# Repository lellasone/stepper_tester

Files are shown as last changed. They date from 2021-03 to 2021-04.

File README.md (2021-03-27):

# stepper_tester
This was a quick one-off stepper tester board. This version uses a TMC2208 from Trinamic. 

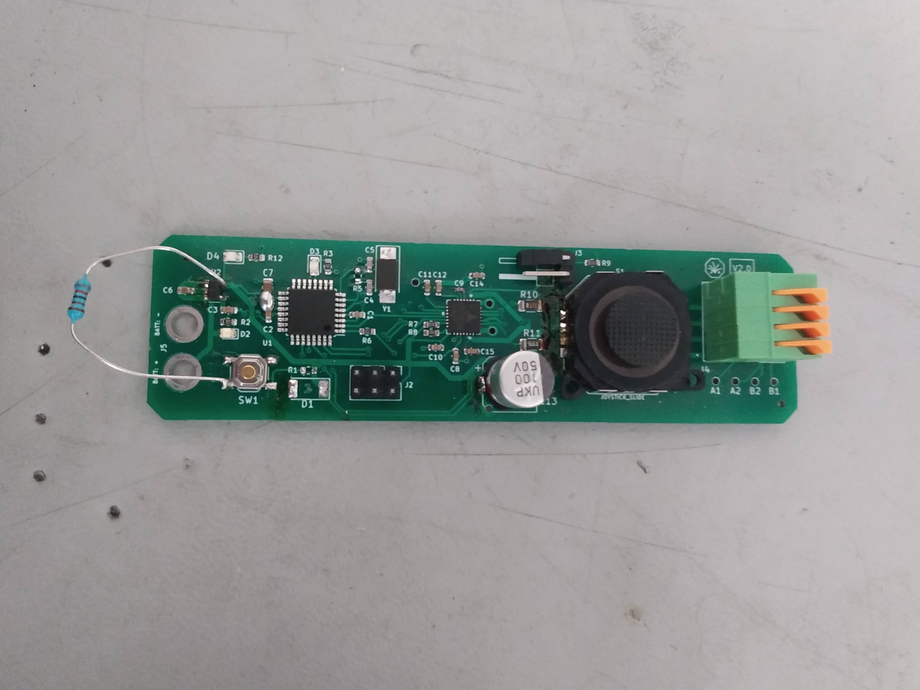
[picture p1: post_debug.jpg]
board just after debug


The idea for this version was to test out if the TMC2208 is really a drop in
replacement for it's competetors in practice (spoiler: it is!). A few (very)
minor improvements have been made to the code, but it actually ran with only
new pin mappings and no other changes the first time I uploaded it.

## Making Changes
For pcb design files look in PCB (KiCAD). For the arduino code look in the 
stepper_driver directory. 

You can upload code to the board using your ISP programmer of choice (I use 
tinyISP) with the fuse settings and pin mappings for a pro-mini.  

## Operating Instructions
* Move the joystick up and down to change the pulse frequency within a single micro-stepping band (zero centered).
* Flick the joystick side to side to change the microstepping level. (faster to the left)
    * To read the current microstepping level, count the status LED's pulses.
* To disable output, connect the jumper by the joystick.

## Firmware Depends
The sketch uses a few Arduino libraries (below) all of which can be 
installed from within the Arduino IDE using the standard library tool.
* PWM Freak - convenience functions for setting pwm devisor values. 
* TIMER1 - convenience functions for timer interrupts

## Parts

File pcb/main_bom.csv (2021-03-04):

Comment | Designator | Footprint | LCSC
100 nF | C1 | Capacitor_SMD:C_0603_1608Metric | C14663
0.1 uf | C10 | Capacitor_SMD:C_0603_1608Metric | C14663
0.22 uF | C11 | Capacitor_SMD:C_0603_1608Metric | C21120
100 uF | C13 | Capacitor_SMD:CP_Elec_8x10
0.1 uF | C2,C8,C12,C14,C15 | Capacitor_SMD:C_0603_1608Metric | C14663
10 nF | C3 | Capacitor_SMD:C_0603_1608Metric | C57112
22pF | C4,C5 | Capacitor_SMD:C_0603_1608Metric | C1653
1uF | C6 | Capacitor_SMD:C_0603_1608Metric | C15849
2.2 uF | C7 | Capacitor_SMD:C_0805_2012Metric | C49217
0.022 uF | C9 | Capacitor_SMD:C_0402_1005Metric | C1532
D | D1 | Diode_SMD:D_2010_5025Metric | C412437
LED | D2 | Diode_SMD:D_0603_1608Metric | C84256
LED | D3,D4 | Diode_SMD:D_0805_2012Metric | C2293
BATT + | J1 | BANANA_CONN
Conn_02x03_Odd_Even | J2 | Connector_PinHeader_2.54mm:PinHeader_2x03_P2.54mm_Vertical
Enable Jumper | J3 | Connector_PinHeader_2.54mm:PinHeader_1x02_P2.54mm_Horizontal
TBL003-254-04GR-2OR | J4 | footprints:header
BATT: - | J5 | BANANA_CONN
10k | R1,R7 | Resistor_SMD:R_0603_1608Metric | C22859
0.1 | R10,R11 | Resistor_SMD:R_1206_3216Metric | C25334
1.2k | R2,R6 | Resistor_SMD:R_0603_1608Metric | C22765
510 | R3,R12 | Resistor_SMD:R_0603_1608Metric | C23193
1M | R5 | Resistor_SMD:R_0603_1608Metric | C22935
100k | R8,R9 | Resistor_SMD:R_0603_1608Metric | C25803
JOYSTICK_SLIDE | S1 | sparkfun_switches:JOYSTICK-PSP1000
SW_Push | SW1 | Button_Switch_SMD:SW_SPST_TL3342
ATmega328P-AU | U1 | Package_QFP:TQFP-32_7x7mm_P0.8mm | C14877
LP2985-5.0 | U2 | Package_TO_SOT_SMD:SOT-23-5
TMC2208 | U3 | QFN28 | C115944
Crystal | Y1 | Crystal:Crystal_SMD_5032-2Pin_5.0x3.2mm_HandSoldering | C115962

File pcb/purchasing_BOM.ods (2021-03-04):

Part Numbers | Value | Footprint | Source | ID
C12, C10, C14, C15, C8, C1, C2 | 0.1uF | 603 | JLC | C14663 (https://lcsc.com/product-detail/Multilayer-Ceramic-Capacitors-MLCC-SMD-SMT_100nF-104-10-50V_C14663.html/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)
C3 | 10nF | 603 | JLC | C57112 (https://lcsc.com/product-detail/Multilayer-Ceramic-Capacitors-MLCC-SMD-SMT_10nF-103-10-50V_C57112.html/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)
C6 | 1uF | 603 | JLC | C15849 (https://lcsc.com/product-detail/Multilayer-Ceramic-Capacitors-MLCC-SMD-SMT_SAMSUNG_CL10A105KB8NNNC_1uF-105-10-50V_C15849.html/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)
C7 | 2.2uF | 805 | JLC | C49217 (https://lcsc.com/product-detail/Multilayer-Ceramic-Capacitors-MLCC-SMD-SMT_2-2uF-225-20-50V_C49217.html/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)
C9 | 0.022uF | 402 | JLC | C1532 (https://lcsc.com/product-detail/Multilayer-Ceramic-Capacitors-MLCC-SMD-SMT_22nF-223-10-50V_C1532.html/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)
C13 | 100uF | 8.3x8.3mm | Digikey | 1189-3099-2-ND
C11, | 0.22uF | 603 | JLC | C21120 (https://lcsc.com/product-detail/Multilayer-Ceramic-Capacitors-MLCC-SMD-SMT_SAMSUNG_CL10B224KA8NNNC_220nF-224-10-25V_C21120.html/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)
D3 | Blue LED | 805 | JLC | C2293
D2 | Red LED | 805 | JLC | C84256
D4 | Green LED | 805 | JLC | C63855
D1 | Protection Diode |  | JLC | C412437 (https://lcsc.com/product-detail/Diodes-Rectifiers-Fast-Recovery_MDD-Microdiode-Electronics-US1MG_C412437.html/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)
R10, R11 | 0.1Ohms | 1206 | JLC | C25334 (https://lcsc.com/product-detail/Chip-Resistor-Surface-Mount_Uniroyal-Elec-1206W4F100LT5E_C25334.html/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)
R1, R7 | 10k | 603 | JLC | C22859 (https://lcsc.com/product-detail/Chip-Resistor-Surface-Mount_Uniroyal-Elec-0603WAF100JT5E_C22859.html/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)
C4, C5, | 22pF | 603 | JLC | C1653 (https://lcsc.com/product-detail/Multilayer-Ceramic-Capacitors-MLCC-SMD-SMT_SAMSUNG_CL10C220JB8NNNC_22pF-220-5-50V_C1653.html/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)
R12, R3 | 510Ohms | 603 | JLC | C23193 (https://lcsc.com/product-detail/Chip-Resistor-Surface-Mount_Uniroyal-Elec-0603WAF5100T5E_C23193.html/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)
R2, R6 | 1.2k | 603 | JLC | C22765 (https://lcsc.com/product-detail/Chip-Resistor-Surface-Mount_Uniroyal-Elec-0603WAF1201T5E_C22765.html/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)
R5 | 1M | 603 | JLC | C22935 (https://lcsc.com/product-detail/Chip-Resistor-Surface-Mount_Uniroyal-Elec-0603WAF1004T5E_C22935.html/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)
R8, R9 | 100k | 603 | JLC | C25803 (https://lcsc.com/product-detail/Chip-Resistor-Surface-Mount_Uniroyal-Elec-0603WAF1003T5E_C25803.html/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)
S1 | Slide Joystick |  | Digikey | 1568-1848-ND
U1 | 328p | TQFP-32_7.0x7.0x0.8P | JLC | C14877 (https://lcsc.com/product-detail/ATMEL-AVR_ATMEL_ATMEGA328P-AU_ATMEGA328P-AU_C14877.html/?href=jlc-SMT)
U3 | TMC2208 | QFN-28_EP_5.0x5.0x0.5P | JLC | C115944 (https://lcsc.com/product-detail/Motor-Drivers_TRINAMIC_TMC2208-LA-T_TMC2208-LA-T_C115944.html/?href=jlc-SMT)
U2 | LP2985-5.0 | SOT23 | Digikey | LP2985AIM5-5.0
Y1 | Crystal | SMD-5032_2P | JLC | C115962 (https://lcsc.com/product-detail/SMD-Crystal-Resonators_Yangxing-Tech-X50328MSB2GI_C115962.html/?href=jlc-SMT)
J2 | 2x3 pin header | 2.54mm | Digikey | 952-2121-ND
J3 | 1x2 bent headder | 2.54mm | Home | Already Have
J4 | 1x4 snap | 2.54mm | Digikey | 102-6387-ND
Jumper | Jumpuer | 2.54mm | Digikey | 952-2165-ND‎
Increase 5V buss width.

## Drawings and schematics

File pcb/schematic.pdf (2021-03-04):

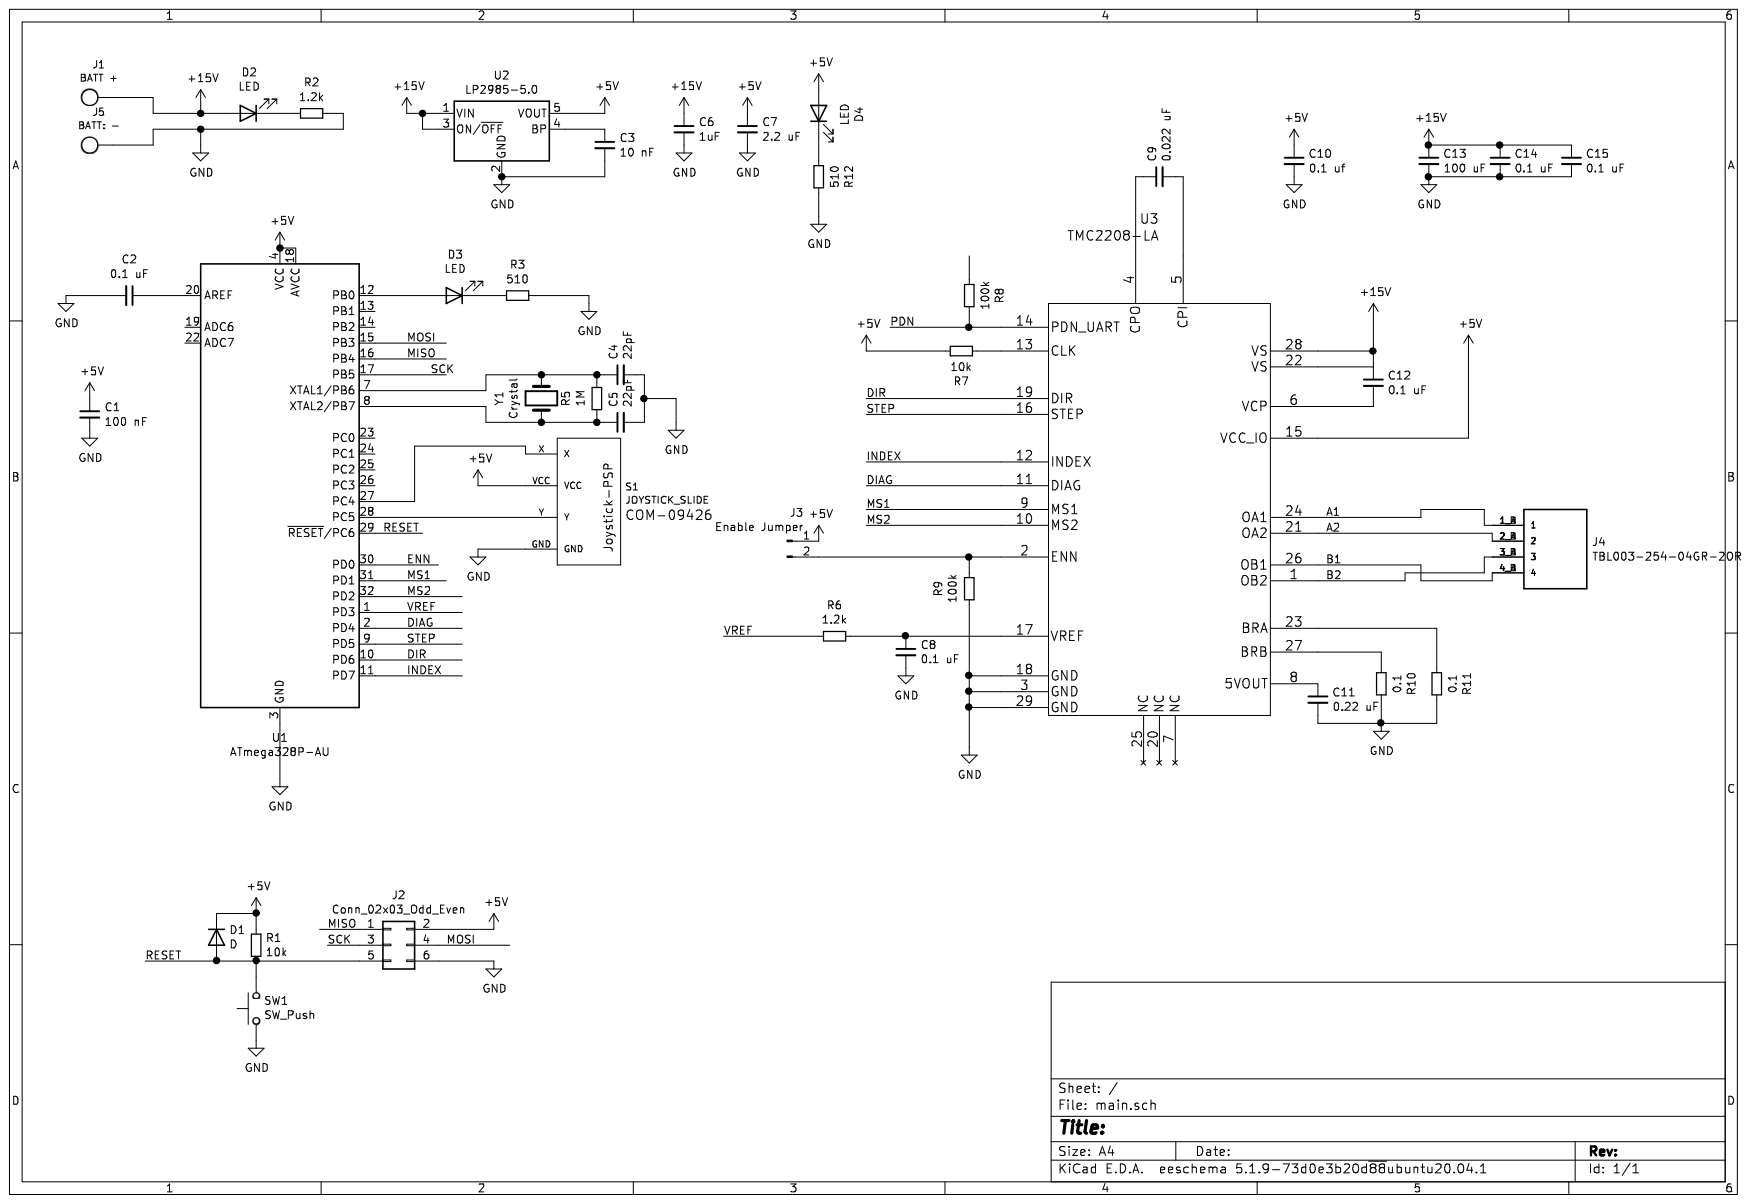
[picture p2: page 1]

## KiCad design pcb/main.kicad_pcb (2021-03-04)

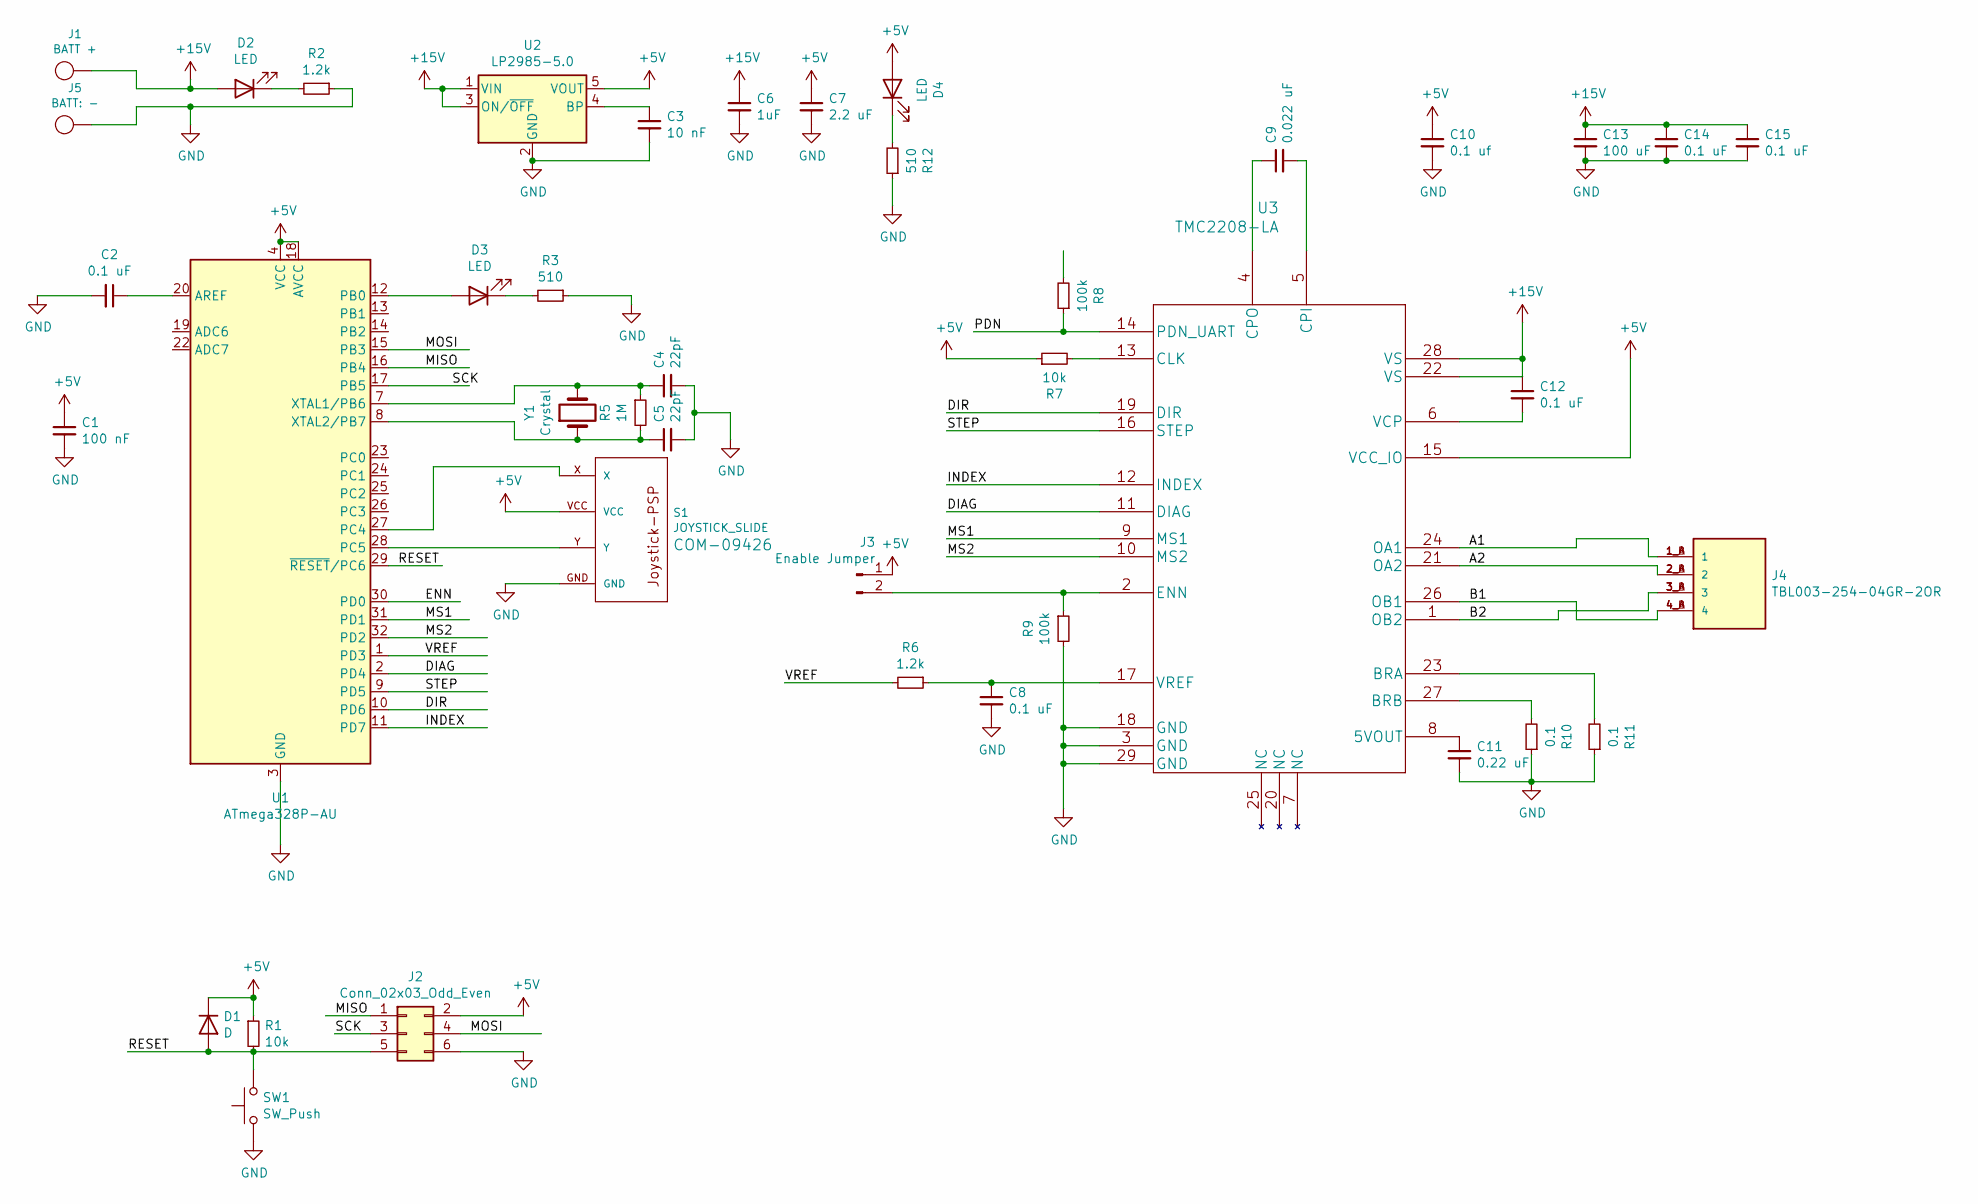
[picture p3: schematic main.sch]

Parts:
C1: 100 nF; C_0603_1608Metric; LCSC C14663
C2, C8, C12, C14, C15: 0.1 uF; C_0603_1608Metric; LCSC C14663
C3: 10 nF; C_0603_1608Metric; LCSC C57112
C4, C5: 22pF; C_0603_1608Metric; LCSC C1653
C6: 1uF; C_0603_1608Metric; LCSC C15849
C7: 2.2 uF; C_0805_2012Metric; LCSC C49217
C9: 0.022 uF; C_0402_1005Metric; LCSC C1532
C10: 0.1 uf; C_0603_1608Metric; LCSC C14663
C11: 0.22 uF; C_0603_1608Metric; LCSC C21120
C13: 100 uF; CP_Elec_8x10
D1: D; D_2010_5025Metric; LCSC C412437
D2: LED; D_0603_1608Metric; LCSC C84256
D3: LED; D_0805_2012Metric; LCSC C2293
D4: LED; D_0805_2012Metric; LCSC C63855
J1: BATT +; BANANA_CONN
J2: Conn_02x03_Odd_Even; PinHeader_2x03_P2.54mm_Vertical
J3: Enable Jumper; PinHeader_1x02_P2.54mm_Horizontal
J4: TBL003-254-04GR-2OR; header
J5: BATT: -; BANANA_CONN
R1, R7: 10k; R_0603_1608Metric; LCSC C22859
R2, R6: 1.2k; R_0603_1608Metric; LCSC C22765
R3, R12: 510; R_0603_1608Metric; LCSC C23193
R5: 1M; R_0603_1608Metric; LCSC C22935
R8, R9: 100k; R_0603_1608Metric; LCSC C25803
R10, R11: 0.1; R_1206_3216Metric; LCSC C25334
S1: JOYSTICK_SLIDE; JOYSTICK-PSP1000
SW1: SW_Push; SW_SPST_TL3342
U1: ATmega328P-AU; TQFP-32_7x7mm_P0.8mm; LCSC C14877
U2: LP2985-5.0; SOT-23-5
U3: TMC2208-LA; LCSC C115944
Y1: Crystal; Crystal_SMD_5032-2Pin_5.0x3.2mm_HandSoldering; LCSC C115962

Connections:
+5V: C1.1, C7.1, C10.1, D1.1 (K), D4.2 (A), J2.2, J3.1, R1.1, R7.1, S1.VCC, U1.4 (VCC), U1.6 (VCC), U1.18 (AVCC), U2.5 (VOUT), U3.15 (VCC_IO)
+15V: C6.1, C12.1, C13.1, C14.1, C15.1, D2.2 (A), J1.1, U2.1 (VIN), U2.3 (ON/~OFF~), U3.22 (VS), U3.28 (VS)
/A1: J4.1_A (1), J4.1_B (1), U3.24 (OA1)
/A2: J4.2_A (2), J4.2_B (2), U3.21 (OA2)
/B1: J4.4_A (4), J4.4_B (4), U3.26 (OB1)
/B2: J4.3_A (3), J4.3_B (3), U3.1 (OB2)
/DIAG: U1.2 (PD4), U3.11 (DIAG)
/DIR: U1.10 (PD6), U3.19 (DIR)
/ENN: U1.30 (PD0)
/INDEX: U1.11 (PD7), U3.12 (INDEX)
/MISO: J2.1, U1.16 (PB4)
/MOSI: J2.4, U1.15 (PB3)
/MS1: U1.31 (PD1), U3.9 (MS1)
/MS2: U1.32 (PD2), U3.10 (MS2)
/PDN: R8.1, U3.14 (PDN_UART)
/RESET: D1.2 (A), J2.5, R1.2, SW1.2, U1.29 (~RESET~/PC6)
/SCK: J2.3, U1.17 (PB5)
/STEP: U1.9 (PD5), U3.16 (STEP)
/VREF: R6.2, U1.1 (PD3)
GND: C1.2, C2.2, C3.2, C4.2, C5.2, C6.2, C7.2, C8.2, C10.2, C11.2, C13.2, C14.2, C15.2, J2.6, J5.1, R2.1, R3.1, R9.2, R10.1, R11.1, R12.1, S1.GND, SW1.1, U1.3 (GND), U1.5 (GND), U1.21 (GND), U2.2 (GND), U3.3 (GND), U3.18 (GND), U3.29 (GND)
unnamed: C2.1, U1.20 (AREF)
unnamed: C3.1, U2.4 (BP)
unnamed: C4.1, R5.1, U1.7 (XTAL1/PB6), Y1.2
unnamed: C5.1, R5.2, U1.8 (XTAL2/PB7), Y1.1
unnamed: C8.1, R6.1, U3.17 (VREF)
unnamed: C9.1, U3.4 (CPO)
unnamed: C9.2, U3.5 (CPI)
unnamed: C11.1, U3.8 (5VOUT)
unnamed: C12.2, U3.6 (VCP)
unnamed: D2.1 (K), R2.2
unnamed: D3.1 (K), R3.2
unnamed: D3.2 (A), U1.12 (PB0)
unnamed: D4.1 (K), R12.2
unnamed: J3.2, R9.1, U3.2 (ENN)
unnamed: R7.2, U3.13 (CLK)
unnamed: R10.2, U3.27 (BRB)
unnamed: R11.2, U3.23 (BRA)
unnamed: S1.X, U1.27 (PC4)
unnamed: S1.Y, U1.28 (PC5)

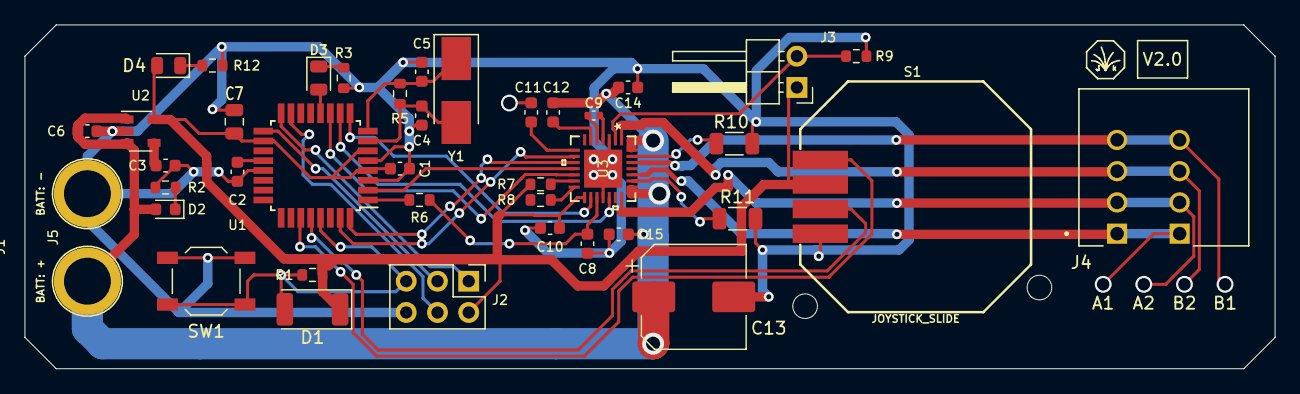
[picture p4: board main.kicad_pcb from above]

Board: 2 copper layers, 101.6 x 27.9 mm, 41 parts (0 on the bottom side), 38 nets.

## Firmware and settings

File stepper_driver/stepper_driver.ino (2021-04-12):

/* 
 *  This is some quick and dirty drive code for my stepper
 *  tester board. It allows speed control and step size 
 *  control based on the joystick, with an expontential 
 *  on the throttle to make control a bit nice. 
 *  
 *  Controls: 
 *  As designed, the stepper tester has throttle
 *  control along it's long axis, with an exponential gain
 *  and a small deadband in the middle. 
 *  
 *  Microstepping is controlled using the short axis, movements
 *  fully to the right will cause an increase in micro-stepping
 *  resulution (if possible) while movements to the left will
 *  cause a decrease. Note that the joystick must return to it's
 *  zero position before another command will be registered. 
 *  
 *  Update: 3/3/2021: Changed pin-mapping to match new board.
 *                    Program with pro-mini settings.
 *  Maintainer: Jake Ketchum
 */

#include "TimerOne.h"

// Hardware Pinouts.
#define PIN_TX     -1
#define PIN_RX     -1
#define PIN_STEP   5
#define PIN_DIR    6
#define PIN_RESET  -1 // reset device, optional. (Not Used)
#define PIN_SLEEP  -1 // dissables output, optional. (Not Used)
#define PIN_FAULT  -1 // should be pulled up. (Not Used)
#define PIN_DECAY  -1
#define PIN_ENABLE 0
#define PIN_HOME   -1 // should be pulled up. (Not Used)
#define PIN_VREF   3
#define PIN_MODE0  1
#define PIN_MODE1  2
#define PIN_MODE2  -1 //(Not Used)
#define PIN_THROTTLE A5
#define PIN_AUX A4
#define PIN_LED 8

// Chip configuration defaults
#define DEFAULT_MODE 0x03
#define DEFAULT_CURRENT 1.7
#define DEFAULT_DECAY HIGH
#define DEFAULT_DIR false

#define CURRENT_MIN 0
#define CURRENT_MAX 2

#define MODE_MIN 0x00
#define MODE_MAX 0x03

#define CURRENT_SENSE_RESISTOR 0.1

#define DEADBAND_HALF 20
#define DEADBAND_CENTER 522



//set the scaling endpoints for the throttle joystick. 
#define THROTTLE_MAX 825
#define THROTTLE_MIN 235 
#define MAX_ACCEL   .25 //The maximum acceleration allowed in rps/s
#define STEPS_PER_REV 200.0 //steps per revolution of the motor.
                          //Scales MAX_ACCEL.
#define MICROS_PER_SECOND 1000000.0

// Speed limits. (rotations per second)
#define MAX_VEL 1.5
#define MIN_VEL 0.1

// Timing defines. 
#define PERIOD_T1  1000000.0 // period of timer 1 in microseconds. 
#define PERIOD_LED  500000.0 // Period of status LED function.
#define PERIOD_POLL  10000.0 // Period for joystick input.


double step_flag = false; // Determine if motor should be moving
int compare = 5;
byte mode = DEFAULT_MODE;

void setup() {
  // put your setup code here, to run once:
  set_pins();
  set_enable(true);
  Timer1.initialize(PERIOD_T1);
  Timer1.attachInterrupt(step_motor,PERIOD_LED);
}

void loop() {
  static int timer = 0;
  int new_time = micros();
  if (new_time - timer > PERIOD_POLL){
    timer = new_time;
    poll_joystick();
  }
  delayMicroseconds(PERIOD_POLL/5);
};

/* 
 *  This function polls the joystick for changes to the 
 *  user specified step frequency and microstepping mode.
 *  The status led update is also called from within this
 *  function.
 *  (This is in place of a "loop()" function)
 */
void poll_joystick()
{

  static unsigned long timer = 0; 
  static int count = 0;
  static int throttle_old = -1;

  update_mode();  // Set the microstepping mode.

  // Get throttle value and pin if outside range.
  
  int throttle = analogRead(PIN_THROTTLE); 
  if (throttle_old != throttle)
  {
    if(throttle > THROTTLE_MAX) throttle = THROTTLE_MAX-1;
  
    if(throttle < DEADBAND_CENTER - DEADBAND_HALF){
      if(throttle < THROTTLE_MIN) throttle = THROTTLE_MIN+1;
      throttle = THROTTLE_MIN;
      double vel = map(throttle, DEADBAND_CENTER, THROTTLE_MIN, MIN_VEL, MAX_VEL);
      set_velocity(vel, false);
    }
    else if (throttle > DEADBAND_CENTER + DEADBAND_HALF){
      double vel = map(throttle, DEADBAND_CENTER, THROTTLE_MAX, MIN_VEL, MAX_VEL);
      set_velocity(MAX_VEL, true);
    }
    else {
      step_flag = false;
    }
  }
  throttle_old = throttle;
  if(count>PERIOD_LED/PERIOD_POLL)
  {
    show_mode();
    count = 0;
  }
  count++;
}

/* 
 *  This function enforces the acceleration limit on velocity
 *  changes and then sets the step frequency and direction pin. 
 *  Note: Accelerations are in terms of rotations/(minute * second)
 *  args:
 *    vel - the new velocity to set. 
 *    forward - if true the direction will be set forward. 
 */
void set_velocity(double vel, double forward){
  static double old_vel = 0;
  if (!step_flag) old_vel = 0;
  const double accel_limit = MAX_ACCEL / (MICROS_PER_SECOND / PERIOD_POLL);
  if (vel > old_vel + accel_limit) vel = old_vel + accel_limit;
  const double period = MICROS_PER_SECOND/(vel*STEPS_PER_REV*mod_mult());
  set_step_period(period, forward);
  old_vel = vel;
}

/*
 * This function sets the step waveform period and direction line. 
 * It will enforce the maximum acceleration constraint. 
 * args:
 *    period - the desired delay between subsiquent step pules in microseconds.
 *    forward - if true the motor will be sent forward. 
 */
double set_step_period(double period, bool forward){
  Timer1.setPeriod(period/2); // 1/2 for interrupt design
  digitalWrite(PIN_DIR, forward); 
  step_flag = true;
  return(period);
}

/* 
 *  Gets the current value of the microstepping mode as a base-10 value. 
 *  This will need to be changed for each chip, though most are just
 *  2^(mode) or 2^(mode + 1).
 */
int mod_mult(){
  switch(mode){
    case 0x00:
      return(2.0);
    case 0x01:
      return(4.0);
    case 0x02:
      return(8.0);
    case 0x03:
      return(16.0);
    default:
      return(1.0);
  }
}

/*
 * This function should be called twice per second. It will
 * blink the onboard LED according to the current microstepping
 * level. 
 */
void show_mode(){
  static int timer = 0;
  static int count = 0;
  static bool on = false;
  int new_time = millis();
  if(on){
    digitalWrite(PIN_LED, LOW);
    on = false;
  } else {
    if (count < mode * 2){
      digitalWrite(PIN_LED, HIGH);
      on = true;
    }
  }
  count++;
  if (count > MODE_MAX * 2){
    count = 0;
  }
}

/* This flips the motor step pin. It should be called at twice the
 *  desired motor step frequency. 
 */
void step_motor(){
  if(step_flag) digitalWrite(PIN_STEP, digitalRead(PIN_STEP) ^ 1);
}
/* 
 *  This function sets up the basic pins configuration for the device. 
 *  Once called, the drv8825 will be in a high-power mode, but will
 *  have it's outputs dissabled. 
 *  
 *  Before sending step and direction inputs be sure to enable the device. 
 */
void set_pins(){

  pinMode(PIN_FAULT, INPUT); 
  pinMode(PIN_HOME, INPUT); 
  pinMode(PIN_DECAY, OUTPUT);
  pinMode(PIN_ENABLE, OUTPUT);//
  pinMode(PIN_VREF, OUTPUT); //
  pinMode(PIN_STEP, OUTPUT);
  pinMode(PIN_DIR, OUTPUT);
  pinMode(PIN_RESET, OUTPUT);//
  pinMode(PIN_SLEEP, OUTPUT);//
  pinMode(PIN_MODE0, OUTPUT);//
  pinMode(PIN_MODE1, OUTPUT);//
  pinMode(PIN_MODE2, OUTPUT);//
  pinMode(PIN_LED, OUTPUT);
  pinMode(PIN_TX, OUTPUT);
  pinMode(PIN_RX, OUTPUT);
 
  digitalWrite(PIN_RESET, HIGH); // dissable reset. 
  digitalWrite(PIN_SLEEP, HIGH); 
  digitalWrite(PIN_DIR, DEFAULT_DIR);

  digitalWrite(PIN_RX, LOW); // so we have a gnd reference. 

  set_enable(false);
  set_mode(DEFAULT_MODE);
  set_current(DEFAULT_CURRENT); 
  digitalWrite(PIN_DECAY, DEFAULT_DECAY);
}

/* 
 *  This function handles incrimenting and decrimenting the 
 *  microstepping level when the joystick is moved sideways. 
 *  The joystick must return to it's neutral location before
 *  another movement can be requested. 
 */
void update_mode(){
  static bool flag = true;
  int step_input = analogRead(PIN_AUX);
  if(step_input > 800 && flag && mode > MODE_MIN){
    mode--;
    set_mode(mode);
    flag = false;
  }
  if(step_input < 200 && flag && mode < MODE_MAX){
    mode++;
    set_mode(mode);
    flag = false;
  }
  if(step_input > 400 && step_input < 600){
    flag = true;
  }
}

/*
 * This function is used to set the micro-stepping mode of the 
 * driver chip. It does so by setting the the three mode control
 * pins on the DRV8825. There are 6 options avaliable
 * corresponding to 1/1, 1/2, 1/4, 1/8, 1/16, 1/32 microstepping. 
 * If the mode byte is larger than 5, it will be set to 5 before
 * processing. 
 * 
 * args: 
 *  mode - determins the microstepping level, values 0-5 correspond
 *         to full through 1/32 microstepping. Values above 5 all
 *         correspond to 1/32 microstepping. 
 */
void set_mode(byte mode){
  if(mode > 5) mode = 5;
  digitalWrite(PIN_MODE0, bitRead(mode, 0));
  digitalWrite(PIN_MODE1, bitRead(mode, 1));
  digitalWrite(PIN_MODE2, bitRead(mode, 2));
}

/* 
 *  This function sets the vref gpio pin to correspond to the 
 *  desired drive current. 
 *  args: 
 *    current - desired current setpoint in amps. 
 */
void set_current(double current){
  if(current < CURRENT_MIN) current = 0; 
  if(current > CURRENT_MAX) current = CURRENT_MAX; 
  // From the data sheet
  int voltage = current*2.5*sqrt(2)*(0.030 + CURRENT_SENSE_RESISTOR)/.325; 
  if (voltage>2.5) voltage = 2.5;
  int voltage_output = map(voltage, 0, 5, 0 , 255); 
  analogWrite(PIN_VREF, voltage_output); 
}

/* 
 *  This function enables or dissables the output transistors of the chip. 
 *  It needs to be called after setup, but before the device is used. 
 *  args:
 *    state - Boolean, if True device will be enabled, if false dissabled. 
 */
void set_enable(bool state){
  digitalWrite(PIN_ENABLE, !(state));
}

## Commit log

2019-08-18 initial commit
    adds pcb files, firmware files, and various pieces of documentation
    [Driver.SchDoc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]
2019-08-23 Now working
    Major changes to firmware, minor reworks on pcb.
    [PCB1.PcbDoc]
2021-03-04 added files for trnamic test board 2208
    [main-B_Cu.gbr, main-B_Mask.gbr, main-B_Paste.gbr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]
2021-03-04 deleted a bunch of stuff
    [PCB1.GBL, PCB1.GBO, PCB1.GBP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]
2021-03-04 deleted the last of the DR8825 items
    [Driver.SchDoc, PCB1.PcbDoc]
2021-03-04 added support for the mode readout LED
2021-03-04 fixed magic number in current set function
    [stepper_driver.ino]
2021-03-27 interrupt based stepping enabled, full speed range enabled, still pins to rails too early, and acceleration curves not adequate, current limit insufficient to prevent overheating
    [stepper_driver.ino]
2021-03-30 compress period setting, does not work
    [stepper_driver.ino]
2021-03-30 acceleration working but not tuned, all modes can reach full speed at 5khz max, but some order of reduction may be reversed
    [stepper_driver.ino]
2021-03-31 velocity curve now linear

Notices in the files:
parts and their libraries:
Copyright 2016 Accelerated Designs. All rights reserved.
